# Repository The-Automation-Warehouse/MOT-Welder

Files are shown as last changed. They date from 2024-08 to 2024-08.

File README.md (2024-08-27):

# MOT-Welder

Made as part of Arcade Hack Club

Used github copilot when writing README

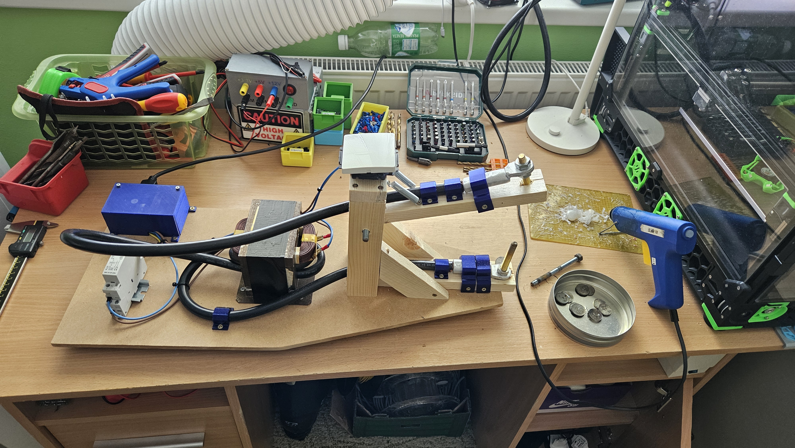
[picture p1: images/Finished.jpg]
Finished project image


In this project, I tried to make a spot welder from modified microwave oven transformer (MOT). But I ended up with more of a metal melter.

## DISCLAIMER
This project involves working with mains voltage electricity and very high current and can be dangerous. I am not responsible for any damage or injury caused by following this project.
Open a microwave oven has killed people before, so proceed at your own risk.
I will not show how to extract and modify the MOT, as there are better and safer guides on the internet.

https://github.com/user-attachments/assets/bb9bf38d-04f5-4f14-8f78-29b9427322f9

## Parts
- 1x Modified MOT
- 1x 230V AC Contactor
- 40mm of DIN rail
- 1x 230V NO Button (I wanted to use a round red one, but I recieved a NC one, so I user a simple light switch)
- 1x 230V Switch
- 1x C13 Socket
- 2x M3x8mm screws
- 1x Wire + ferrules and spade connectors
- 1x 600x250x8mm MD board
- 5x 3D printed Foot
- 2x 3D printed Lug clip
- 4x 3D printed Wire clip
- estimated 2m of 44x19mm wood
- 2x Spring (optional)
- Threaded rod and nuts to fit your wire lugs (USE COPPER ROD, I wanted to save money and ordered it from aliexpress, but I recieved brass and it is slowly melting and it does not conduct the high current well)
- M8 threaded rod
- 2x 608 bearings (optional)
- Bunch of 3.5x12mm and 3.5x16mm screws
- 2x M3 threaded inserts and M3x8mm screws for the cover
- 1x 3D printed cover
- Hot glue

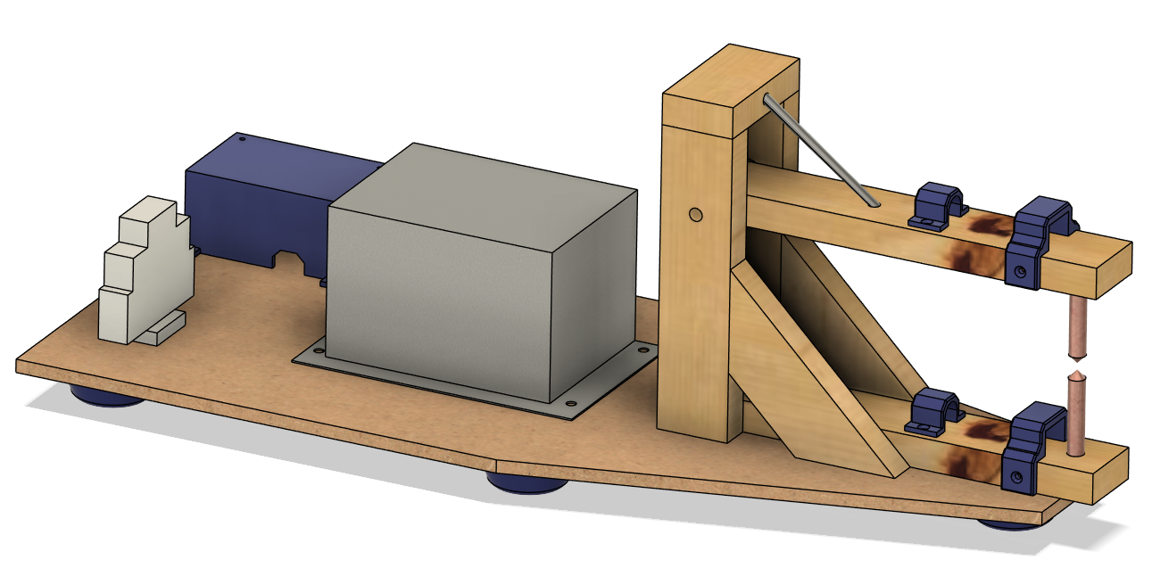
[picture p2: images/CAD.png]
CAD


## Aligning the elctrodes

The better the alignment, the easier the welding. When the electrodes are not aligned, its tricky to hold the parts in place and the welds are not as strong. At first I used hot glue to hold the wire lugs in place, but it got soft and melted on the first use. I then shimmed the bottom electrode with a coin and it worked much better. The top electrode can be adjusted by enlarging the hole in the top wooden arm.

## Schematic

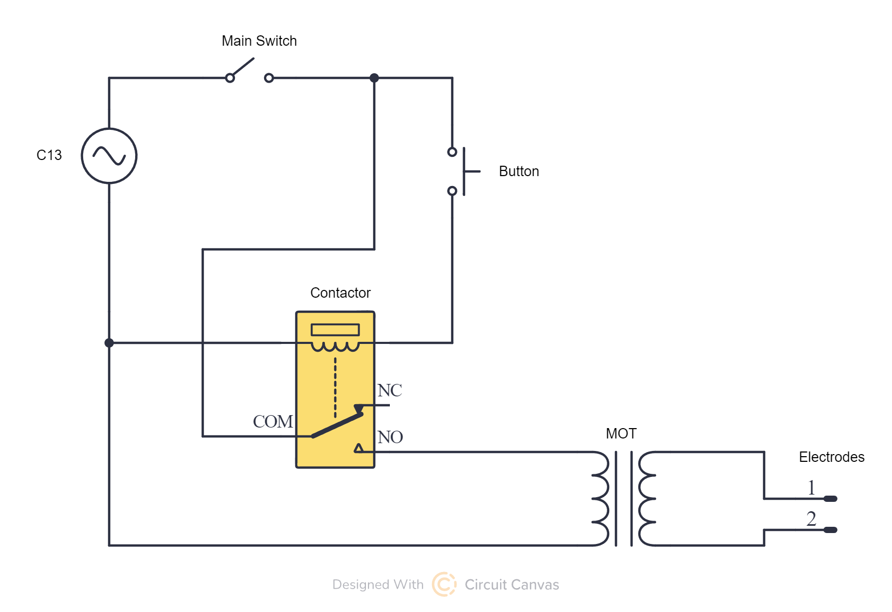
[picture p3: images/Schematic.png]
Schematic


The main switch can cut power to everything, the button is used to activate the contactor. The contactor is switches the mains power to the MOT. The MOT is connected directly to the electrodes.

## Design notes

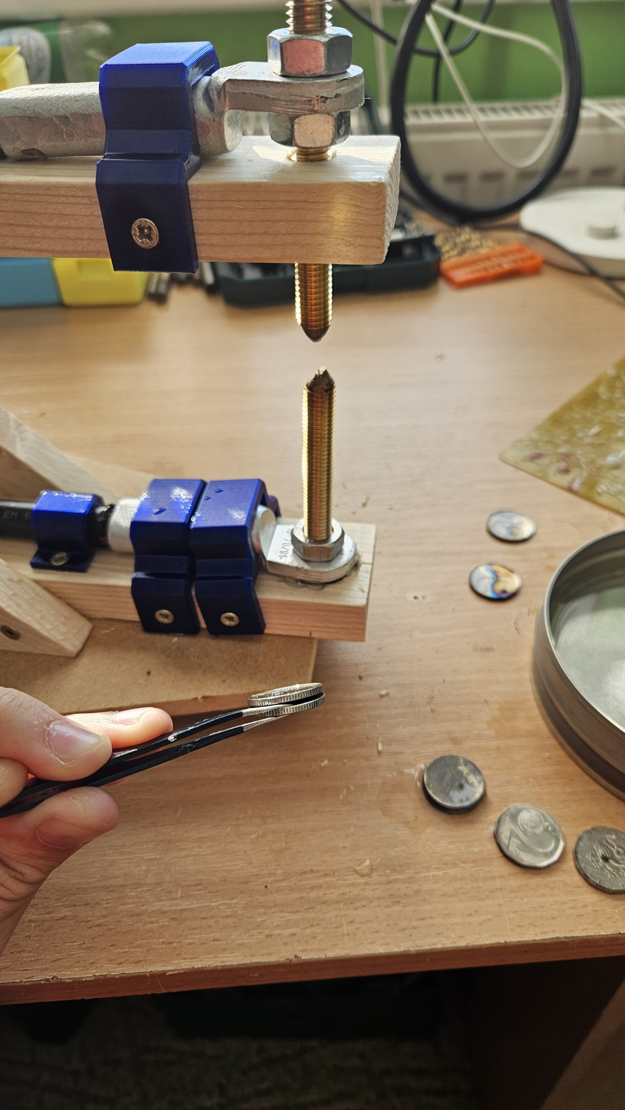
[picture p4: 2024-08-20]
images/Electrodes.jpg

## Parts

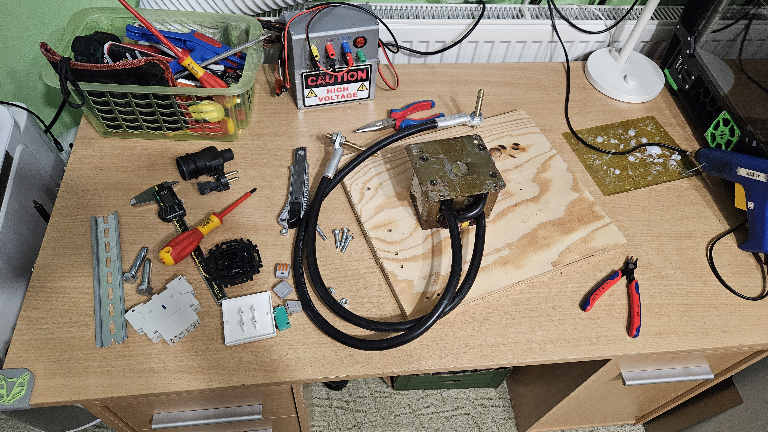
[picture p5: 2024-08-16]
making of/Parts.jpg

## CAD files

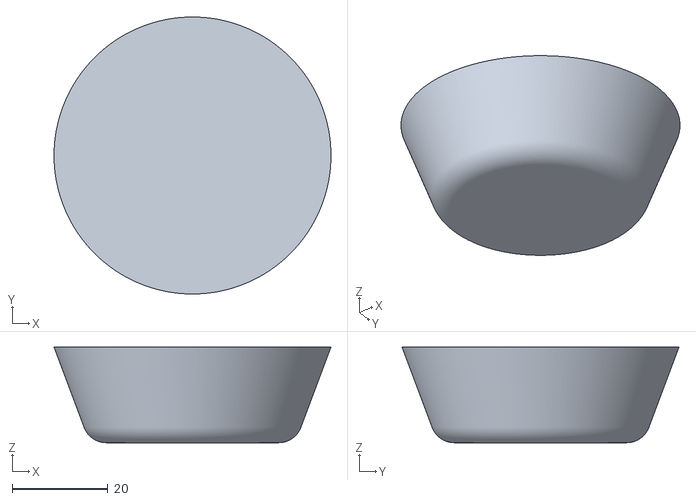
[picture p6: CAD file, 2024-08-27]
CAD/Foot.stl
58.0 x 58.0 x 20.0

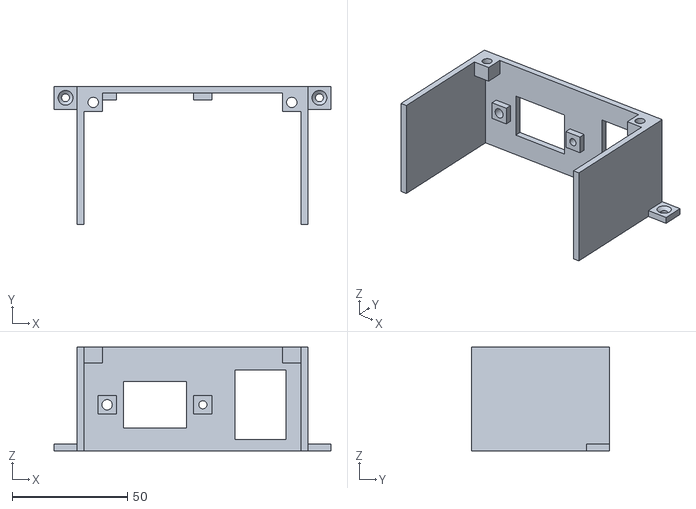
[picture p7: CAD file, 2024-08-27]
CAD/Cover - bottom.stl
120.0 x 60.0 x 45.0

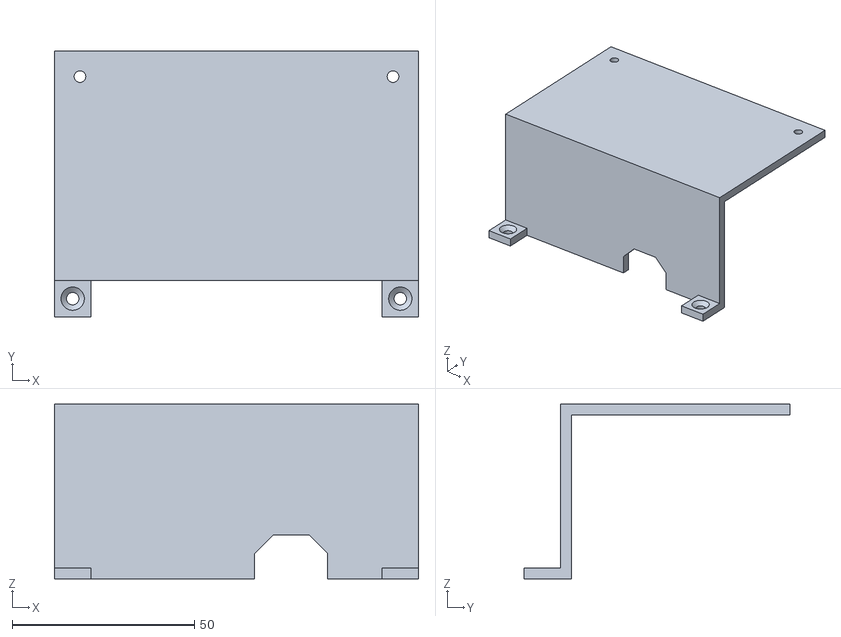
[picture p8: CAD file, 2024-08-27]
CAD/Cover - top.stl
100.0 x 73.0 x 48.0

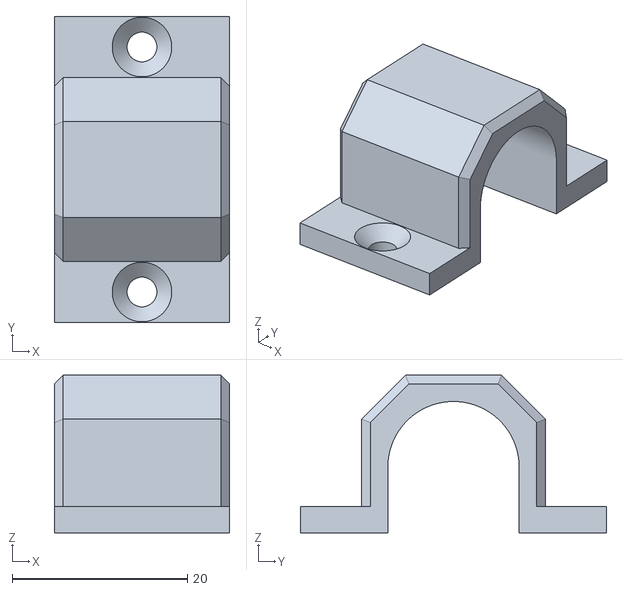
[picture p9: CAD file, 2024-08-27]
CAD/Wire clip.stl
20.0 x 35.0 x 18.0

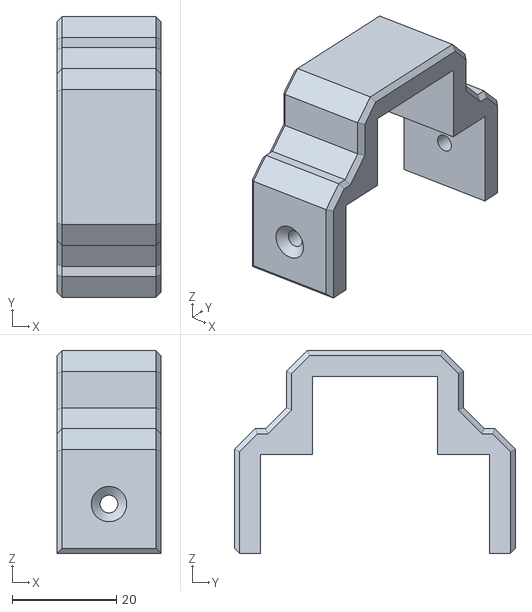
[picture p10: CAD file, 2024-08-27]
CAD/Lug clip.stl
20.0 x 54.0 x 39.0

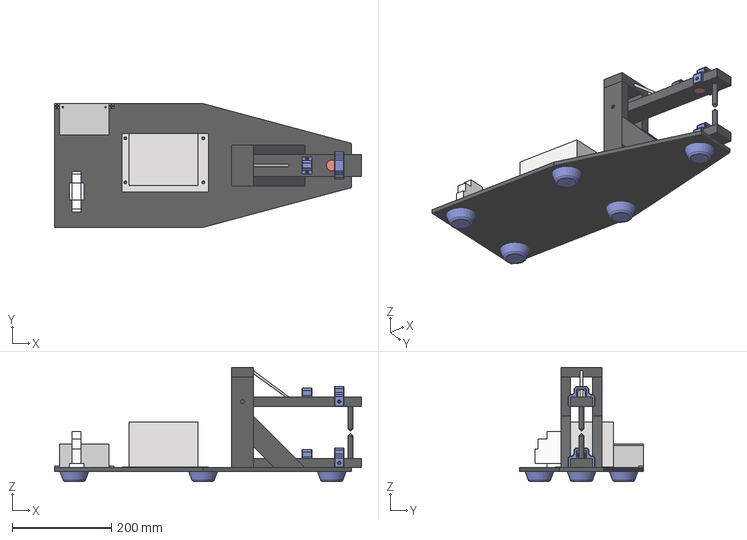
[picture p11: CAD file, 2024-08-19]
CAD/MOT Welder.step
620.0 x 250.0 x 230.5 mm

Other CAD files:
CAD/MOT Welder.3mf
CAD/MOT Welder.f3d

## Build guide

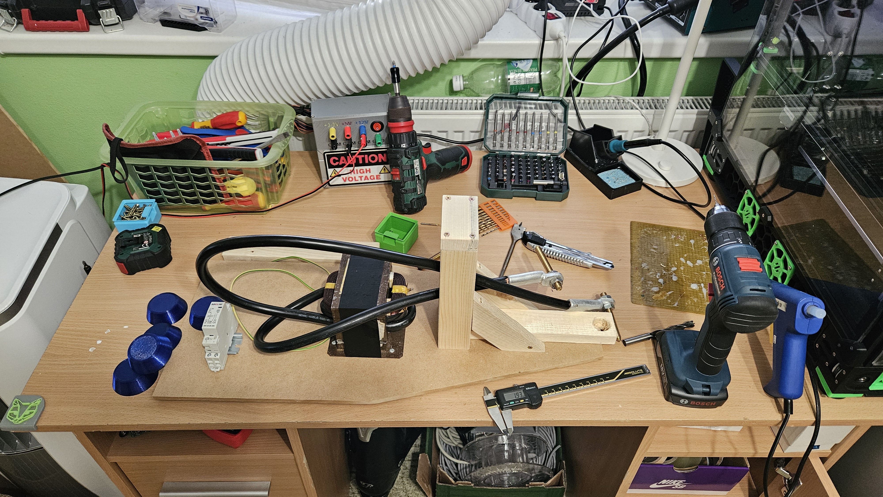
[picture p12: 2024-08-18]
making of/Assembly 2.jpg

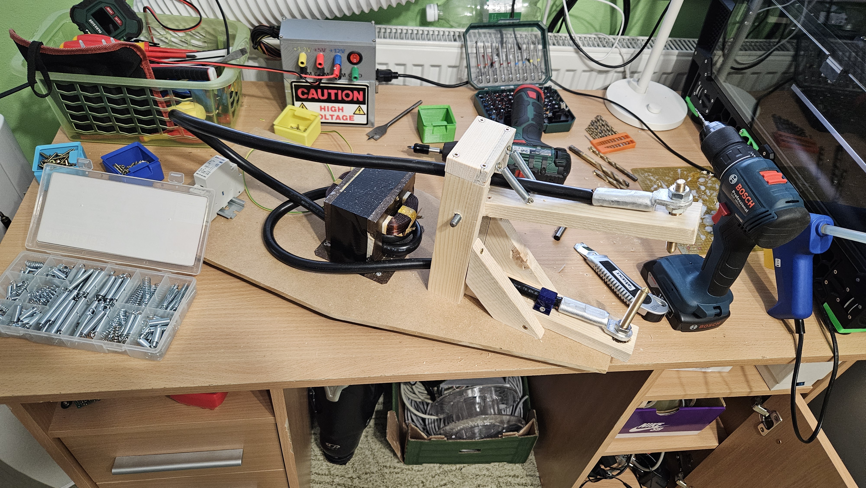
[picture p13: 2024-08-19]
making of/Assembly 3.jpg

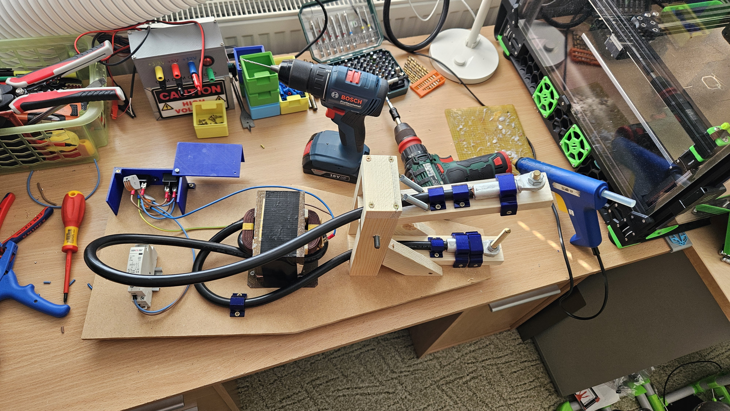
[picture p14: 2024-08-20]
making of/Wiring.jpg

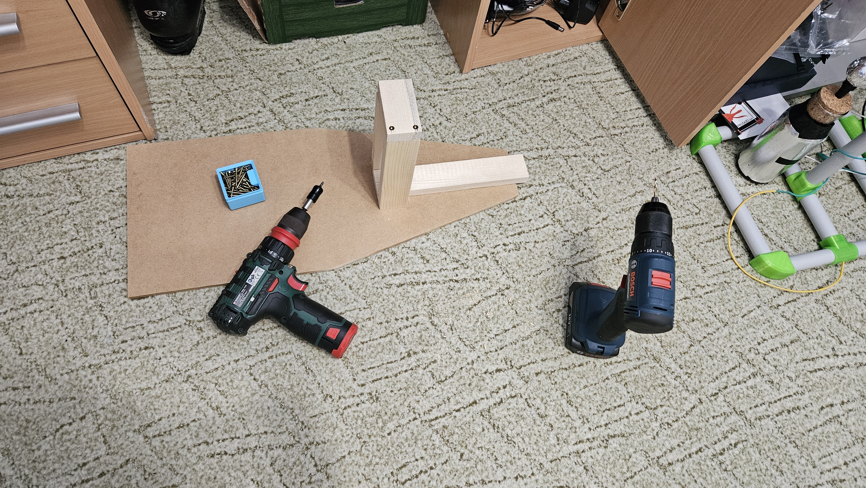
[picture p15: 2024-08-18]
making of/Assembly 1.jpg

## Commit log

2024-08-16 Create MOT Welder.step
    [MOT Welder.step]
2024-08-16 Update MOT Welder.step
    [MOT Welder.step]
2024-08-18 Create Assembly 1.jpg
2024-08-18 Create Assembly 2.jpg
2024-08-19 Create Assembly 3.jpg
2024-08-20 Aligned the electrodes
2024-08-27 Finished the build
    [Cover - bottom.stl, Cover - top.stl, Foot.stl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]
2024-08-27 Documenation update
    [MOT Welder.3mf, MOT Welder.f3d]
